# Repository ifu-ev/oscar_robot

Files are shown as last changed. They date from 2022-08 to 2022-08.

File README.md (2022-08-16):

# oscar_robot

## Content

- [oscar_robot](#oscar_robot)
  - [Introduction](#introduction)
  - [<span style="color:red">**!!! CAUTION !!!**</span>](#-caution-)
  - [Knowledge requirement](#knowledge-requirement)
  - [Shopping-List](#shopping-list)
    - [Budget Build Parts](#budget-build-parts)
    - [Original Build Parts](#original-build-parts)
    - [Laser-cutted parts](#laser-cutted-parts)
    - [3-D printed parts](#3-d-printed-parts)
  - [Build your robot](#build-your-robot)
    - [Hardware installation](#hardware-installation)
      - [Budget Build](#budget-build)
      - [Original Build](#original-build)
  - [Setup software](#setup-software)
    - [Budget Build (Raspberry Pi)](#budget-build-raspberry-pi)
    - [Original Build (Intel NUC)](#original-build-intel-nuc)
    - [Connect to Oscar via SSH](#connect-to-oscar-via-ssh)
    - [Installing ROS](#installing-ros)
    - [OSCAR workspace](#oscar-workspace)
    - [Connect Gamepad](#connect-gamepad)
  - [Usage](#usage)
    - [Teleoperation](#teleoperation)
    - [Mapping](#mapping)
    - [Navigation](#navigation)
  - [Publishing own navigation goals](#publishing-own-navigation-goals)
  - [Credits](#credits)

## Introduction

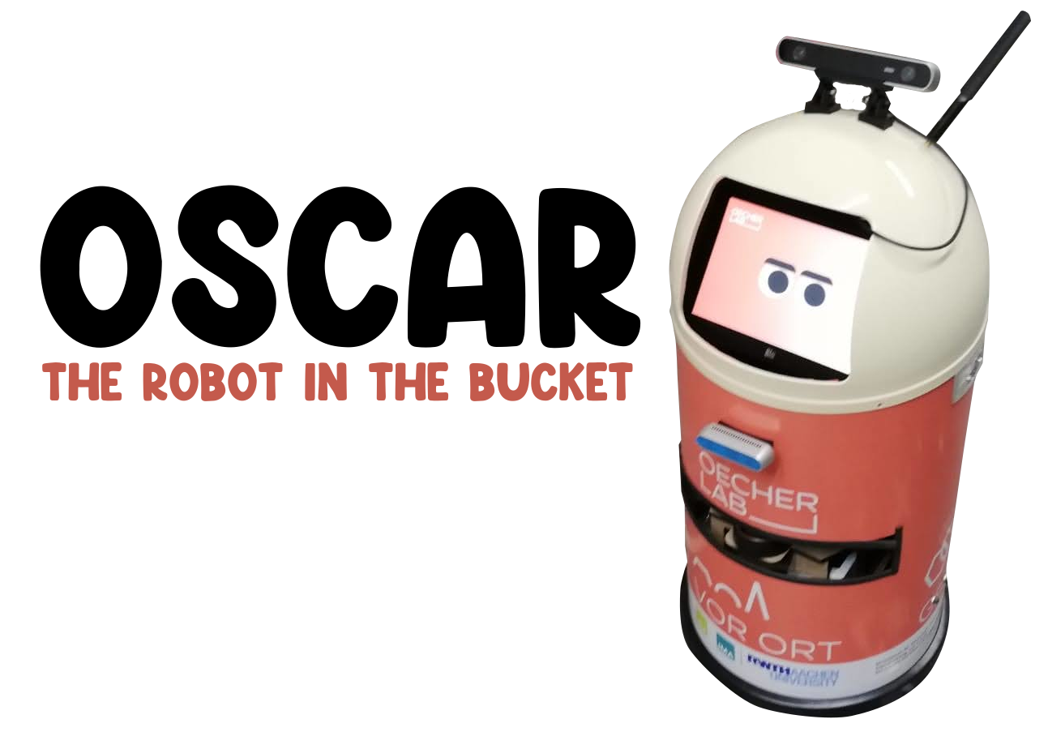
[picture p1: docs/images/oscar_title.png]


The "Oecher Lab" project is funded by the state of NRW, Germany as part of the "Digital Model Regions in NRW" program.

Oscar is a learning robot developed as part of the research project OecherLAB. Oscar is used to teach the Robot Operating System. It owes its name to its outer shell: the garbage can in which a well-known children's hero lives.

This documentation should enable everyone to rebuild and configure the robot, as well as to dare the first steps with ROS.

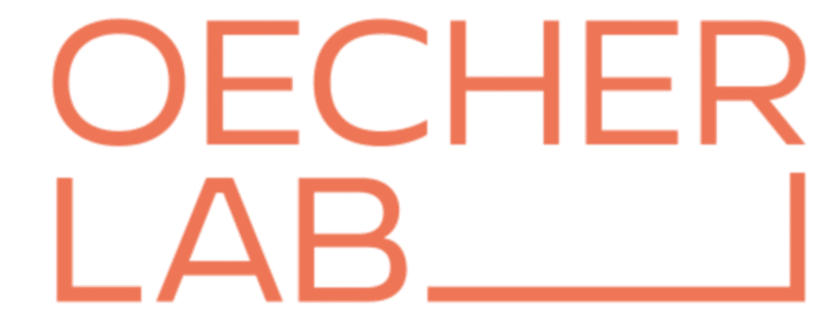
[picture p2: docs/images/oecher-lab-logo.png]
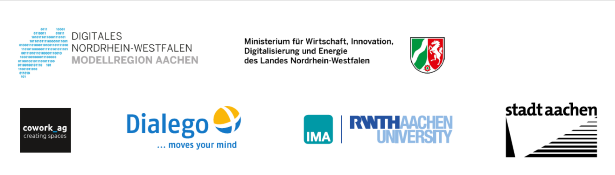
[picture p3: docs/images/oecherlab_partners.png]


https://user-images.githubusercontent.com/32275/184821746-e5f2bd64-7a9f-4834-b20b-766fcd85903a.mp4

<table class="tg">
<thead>
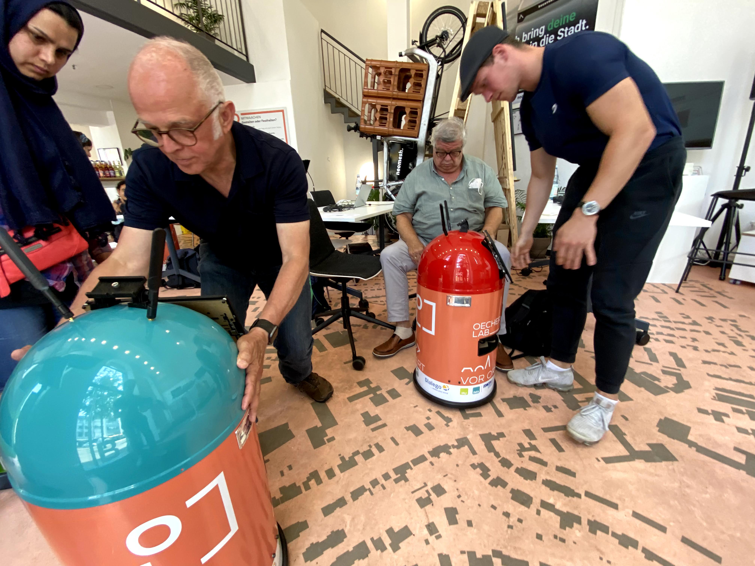
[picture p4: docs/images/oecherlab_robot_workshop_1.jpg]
    <td></td>
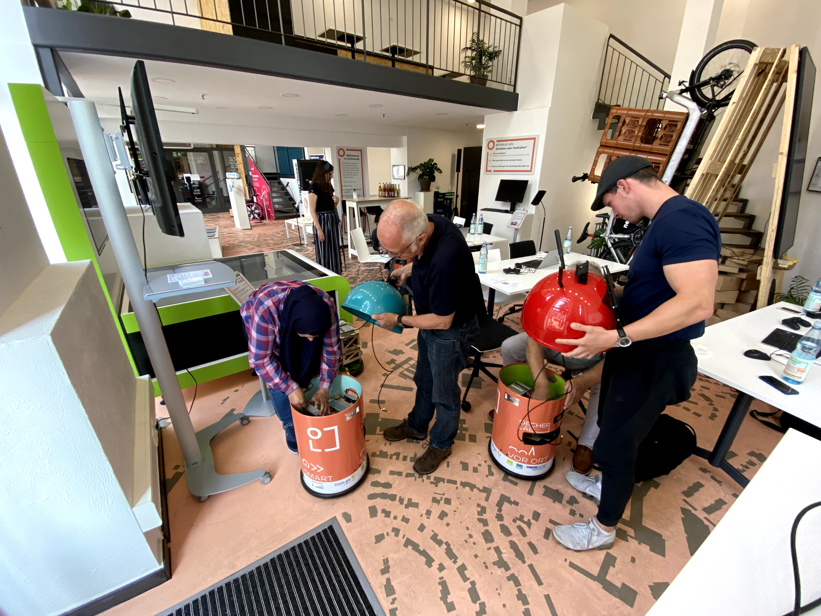
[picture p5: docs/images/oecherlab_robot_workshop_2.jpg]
    <td></td>
</thead>
</table>

---

## <span style="color:red">**!!! CAUTION !!!**</span>

**This tutorial contains instructions for working with electricity, soldering irons and sharp objects. Incorrect handling can lead to serious physical injuries. Please read about how to work safely with these topics before proceeding.**

---

## Knowledge requirement

- basic knowledge in Ubuntu Linux
- basic knowledge in ROS
- manual skills

## Shopping-List

In this chapter we describe the hardware you need to build your own Oscar. We build the Robot with powerful hardware to execute cutting edge algorithms (which are not part of this tutorial). If you just want to build the robot for getting in touch with ROS and the navigation stack, you can choose to build the budget build.

### Budget Build Parts

|Type | Product |
|-----|---|
|Robot Base|iRobot Create 2 (EOL/AfterMarket)|
|Embedded Computer|[RaspberryPi 4 (4GB)](https://www.google.de/search?tbm=shop&hl=de&q=raspberry+pi+4+4gb) + [64GB microSD Card (dont buy fakes from Aliexpress)](https://www.google.de/search?tbm=shop&hl=de&q=64GB+micro+SD+Card)|
|2D Lidar|[RPLidar A2M8](https://www.google.de/search?tbm=shop&hl=de&q=rplidar+a2m8)|
|RGBD Camera|[Intel Realsense d435i](https://www.google.de/search?tbm=shop&hl=de&q=realsense+d435i)|
|Gamepad|[Sony Dualshock 4 Controller](https://www.google.de/search?tbm=shop&hl=de&q=sony+dualshock+4)|
|DC/DC Converter|[Sunfounder Step-down DC-DC Converter Module for Raspberry Pi](https://www.robotshop.com/de/de/sunfounder-step-down-dc-dc-wandlermodul-raspberry-pi.html)|
|USB-C cable|[Generic USB-C Cable](https://www.google.de/search?tbm=shop&hl=de&q=usb-c+cable)|
|USB-A hub|[Generic USB-3.0-hub](https://www.google.de/search?tbm=shop&hl=de&q=usb+a+3.0+hub)|
|Battery|[Turnigy 5000mAh 6S LiPo](https://hobbyking.com/de_de/turnigy-5000mah-6s-40c-lipo-pack-xt90.html)|
|Charger|[Generic 6S LiPo Charger](https://www.google.com/search?q=lipo+charger+b6&source=lmns&tbm=shop)|
|Cable + Plug|[XT90 Plug (male) + cable](https://www.google.de/search?tbm=shop&hl=de&q=xt90+male+with+cable)|

### Original Build Parts

|Type | Product |
|-----|---|
|Robot Base|iRobot Create 2 (EOL/AfterMarket)|
|Roboter Body|[Wesco Pushboy](https://www.google.de/search?tbm=shop&hl=de&q=wesco+pushboy)|
|PC|[Intel NUC](https://www.google.de/search?tbm=shop&hl=de&q=intel+nuc+i5)  + [32GB DDR4-SODIMM 2666MHz](https://www.google.de/search?tbm=shop&hl=de&q=32gb+ddr4+sodimm+2666) + [512GB M2 SSD](https://www.google.de/search?tbm=shop&hl=de&q=32gb+ddr4+sodimm+2666)|
|AI PC|[Nvidia Jetson Nano](https://www.google.de/search?tbm=shop&hl=de&q=nvidia+jetson+nano)|
|Router|[Teltonika RUTX12](https://www.google.de/search?tbm=shop&hl=de&q=teltonika+rutx12)|
|2D Lidar|[RPLidar A2M8](https://www.google.de/search?tbm=shop&hl=de&q=rplidar+a2m8)|
|RGBD Camera|[Intel Realsense d435i](https://www.google.de/search?tbm=shop&hl=de&q=realsense+d435i)|
|Gamepad|[Sony Dualshock 4 Controller](https://www.google.de/search?tbm=shop&hl=de&q=sony+dualshock+4)|
|DC/DC Power Supply|[DCDC-USB, Intelligent DC-DC converter with USB interface](https://www.mini-box.com/DCDC-USB) + [Male DC Plug 5.5mm x 2.1mm](https://www.google.de/search?tbm=shop&hl=de&q=male+dc+plug)|
|Fuse Distribution Board|[Generic Distribution Board](https://www.google.de/search?tbm=shop&hl=de&q=fuse+distribution+board)|
|Molex cable|[Molex MicroFit Cable](https://www.google.de/search?tbm=shop&hl=de&q=4pin+molex+microfit+cable)|
|USB-C cable|[Generic USB-C Cable](https://www.google.de/search?tbm=shop&hl=de&q=usb-c+cable)|
|USB-A hub|[Generic USB-3.0-hub](https://www.google.de/search?tbm=shop&hl=de&q=usb+a+3.0+hub)|
|Ethernet Cable|[Ethernet Cable 0.4m](https://www.google.de/search?tbm=shop&hl=de&q=ethernet+cable)|
|WiFi Antenna Extension|[WiFi Antenna Extension](https://www.google.de/search?tbm=shop&hl=de&q=sma+extension)|
|Battery|[SLS 16000mAh 6S LiPo](https://www.stefansliposhop.de/akkus/sls-multirotor-uav/sls-xtron/sls-xtron-16000mah-6s1p-22-2v-20c-40c::2214.html)|
|Charger|[Generic 6S LiPo Charger](https://www.google.com/search?q=lipo+charger+b6&source=lmns&tbm=shop)|
|Cable + Plug|[XT90 Plug (male) + cable](https://www.google.de/search?tbm=shop&hl=de&q=xt90+male+with+cable)|

### Laser-cutted parts

The Create 2 base from iRobot has mounting points on its top plate. We use these points to attach a self developed lasercutted wooden construction. You can build your own top-construction for the raspberry pi/nuc and sensors, but we also provide the CAD files in the following table. You have to search for a company in your place to cut these parts for you.

Material thickness: 6 mm

| Qty | Type | Download |
|-----|---|---|
|1x|Layer bottom|[Download](docs/cad/layer_bottom.dxf)|
|1x|Layer middle|[Download](docs/cad/layer_middle.dxf)|
|1x|Layer top|[Download](docs/cad/layer_top.dxf)|
|3x|Side standard bottom|[Download](docs/cad/side_standard_bottom.dxf)|
|3x|Side standard top|[Download](docs/cad/side_standard_top.dxf)|
|1x|Side front bottom|[Download](docs/cad/side_front_bottom.dxf)|
|1x|Side front top|[Download](docs/cad/side_front_top.dxf)|

### 3-D printed parts

We provide a STL-File for mounting the Intel Realsense camera to the top plate. You have to print it by yourself or find a company in your area which can print it for you.

| Qty | Type | Download |
|-----|---|---|
|1x|Realsense mount|[Download](docs/cad/realsense_mount.stl)|

## Build your robot

To build your robot is quiet easy. You just have to slide the parts into each other. We recommend to fix the bottom connection of each side plate with hot glue. Screw the bottom plate on the item parts, which work as stands.

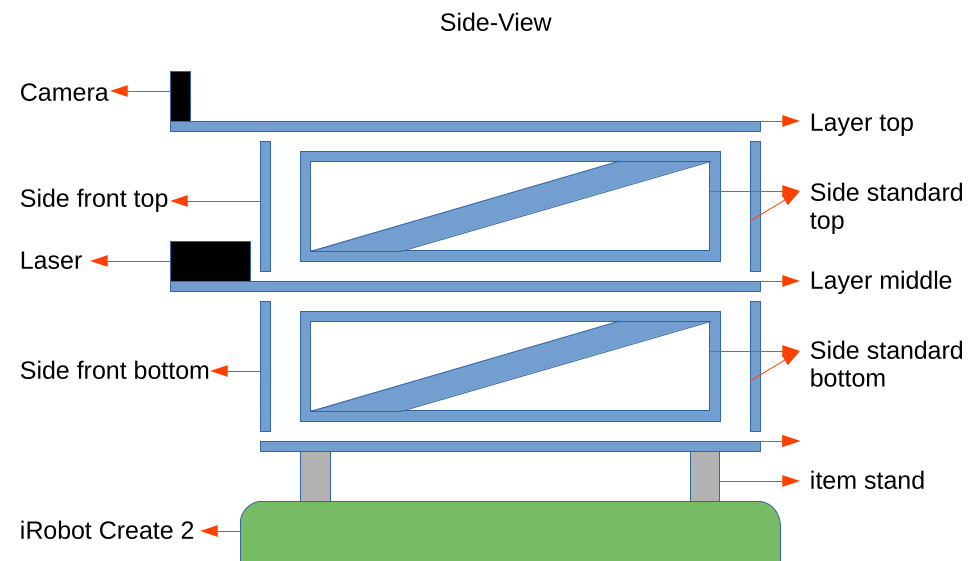
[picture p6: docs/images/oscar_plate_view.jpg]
oscar_plate_view


### Hardware installation

#### Budget Build

- Fix the raspberry pi on one of the layers.
- Connect the USB-C cable to the RaspberryPi and the DC/DC converter
- Prepare the XT90 with cable and connect it to the DC/DC converter
- Mount the Lidar on the front part of the middle plate with screws
- Screw the Realsense camera to the 3D-printed mounting and the mounting on the front of the top plate
- Connect both sensors and the iRobot Create Serial cable to the USB-Hub
- Connect the USB-Hub to the RaspberryPi
- Connect the battery to the DC/DC Converter when you want to run the robot

#### Original Build

- Install the RAM and SSD into the Intel NUC
- Fix the Intel NUC with the provided mounting plate (in package) to the "side standard top" with power button facing front
- Fix the Nvidia Jetson Nano on the middle plate
- Mount the Lidar on the front part of the middle plate with screws
- Screw the Realsense camera to the 3D-printed mounting and the mounting on the front of the top plate
- Mount the DC/DC Converter on the top plate
- Solder the XT90 with cables from package and connect it to the DC/DC converter
- Mount the fuse distribution board on bottom plate and connect the DC/DC converter
- Solder Cables with male DC plugs for powering Intel NUC and Nvidia Jetson Nano
- Connect the molex cable to the Teltonika RUTX12 and the distribution board
- Connect both sensors and the iRobot Create Serial cable to the USB-Hub
- Connect the USB-Hub to the Intel NUC
- Connect the battery to the DC/DC Converter when you want to run the robot
- Carefully remove the rivets holding the head together with the body of the pushboy using a small drill bit
- Use a lathe tool to cut a horizontal slit at the level of the RPLidar laser with an opening angle of approximately 160 degrees
- Cut a smaller opening for the Intel Realsense Camera on its height
- Drill a hole in the head for the SMA extension
- Hot-Glue the 3D-printed holders in the inside
- You can put the Pushboy on the Roomba as external chassy

## Setup software

- Install [Ubuntu 20.04 Desktop](https://releases.ubuntu.com/20.04/) on your local machine.

### Budget Build (Raspberry Pi)

- Download the [Raspbery Pi Imager](https://www.raspberrypi.com/software/)
- Start Imager
- Choose OS -> other general-purpose OS -> Ubuntu -> Ubuntu Server 20.04 LTS 64bit
- Insert the microSD into an SD Adapter and put it in your SD Card reader
- Choose Storage -> select microSD
- Click on the settings button
  - set hostname: oscar.local
  - enable ssh -> use password; username: oscar, pw: oscar
  - configure your local Wifi
  - configure your locale settings (timezone, keyboard)
  - save
- click on "Write"
- insert the sd card to your raspberry pi and turn it on
- the raspberry pi should connect to your wifi automatically

### Original Build (Intel NUC)

- Configure your [Teltonika RUTX12 to connect to your local Wifi](https://wiki.teltonika-networks.com/view/RUTX12)
- Download [Ubuntu 20.04 Desktop](https://releases.ubuntu.com/20.04/)
- Create a bootable USB Stick with your favourite flash tool (e.g. Rufus / Etcher)
- Put the stick in your Intel NUC
- Connect
- Connect a mouse, keyboard and monitor
- Start the Intel NUC and enter one-time boot menu
- Select the USB Drive in UEFI Mode
- Go through Ubuntu Installer
  - Username: oscar, pw: oscar
  - PC-Name: oscar

### Connect to Oscar via SSH

- Windows-User (you can connect via SSH, but you cannot visualize later on):
  - [Install PuTTY](https://www.chiark.greenend.org.uk/~sgtatham/putty/latest.html)
  - Start PuTTY
    - Host Name: oscar.local
    - Port: 22
  - Click "Open"
  - login as: `oscar`
- Linux-User:
  - Open your terminal (Ctrl + Shift + T)
  - `ssh oscar@oscar.local`
- Type in the password: `oscar` (passwords are not shown in the terminal)

### Installing ROS

- The next steps are slightly modified from original ROS installation ([ROS-WIKI](http://wiki.ros.org/noetic/Installation/Ubuntu))
- The commands have to be executed on the remote system over SSH connection AND on your local machine too (you have to do it twice)
  - `sudo sh -c 'echo "deb http://packages.ros.org/ros/ubuntu $(lsb_release -sc) main" > /etc/apt/sources.list.d/ros-latest.list'`
  - `sudo apt install curl`
  - `curl -s https://raw.githubusercontent.com/ros/rosdistro/master/ros.asc | sudo apt-key add -`
  - `sudo apt update && sudo apt dist-upgrade`
  - `sudo apt install ros-noetic-desktop-full`
  - `echo "source /opt/ros/noetic/setup.bash" >> ~/.bashrc`
  - `source ~/.bashrc`
  - `sudo apt install python3-rosdep python3-rosinstall python3-rosinstall-generator python3-wstool build-essential python3-catkin-tools vim screen`
  - `sudo rosdep init`
  - `rosdep update`
- We have to add the param `ROS_MASTER_URI` and `ROS_IP` to our `~/.bashrc` file on the remote and local machine
- Get the IPv4 of your remote and local machine
  - `ifconfig`
- Edit your `.bashrc`
  - `vim ~/.bashrc`
- Go to the bottom of the file with the arrow keys
- Enter Insert-Mode by hitting the key `i`
  - `ROS_MASTER_URI=http://<insert IP of NUC/Raspberry here>:11311` e.g. `ROS_MASTER_URI=http://192.168.0.100:11311`
  - `ROS_IP=<IP of the system you are working on>`
- Exit insert mode by hitting `ESC`
- Save your changes
  - `:wq` write and quit

### OSCAR workspace

- Now we install the oscar related packages and compile them
  - `mkdir -p ~/oscar_ws/src`
  - `cd ~/oscar_ws/src`
  - `git clone https://github.com/ifu-ev/oscar_robot`
  - `cd ..`
  - `rosdep install --from-paths src --ignore-src -r`
  - `catkin build`
  - `echo "source ~/oscar_ws/devel/setup.bash" >> ~/.bashrc`
  - `source ~/.bashrc`
  - `roscd oscar_bringup/udev`
  - `source create_udev_rules.sh`

### Connect Gamepad

- Connect to your remote machine via SSH
- Put your gamepad in pairing mode (Dualshock: Hold share and Playstation button until white light is flashing)
- `sudo bluetoothctl`
- `scan on`
- Wait until you see a Sony label
- `scan off`
- Copy the MAC address (this is an example mac address `4C:E9:9A:43:C7:2A`)
- `trust '<here your mac address'`
- `connect '<here your mac address'`
- The controller should be connected now

## Usage

To start the Oscar the ROS package oscar_bringup exists. In this package are all necessary launch files, which start the hardware drivers and the algorithms needed for the task.

### Teleoperation

- With the launch file `teleoperation.launch` the robot can be operated manually with the controller.
- `roslaunch oscar_bringup teleoperation.launch`

### Mapping

- With the launch file `mapping.launch` we can create a map for later autonomous navigation with the Oscar.
- Start the mapping on the remote machine
  - `roslaunch oscar_bringup mapping.launch`
- Start the Visualization on your local machine
  - `roslaunch oscar_bringup visualization.launch`
- Click on `2D Nav Goal` and set a goal pose on the map in the 3D view with your mouse
- The robot will move to that position
- The mapping algorithm is generating the map from the 2D lidar scanner
- We can use this map later for navigation tasks
- Save the map on your oscar robot
  - `roslaunch oscar_navigation save_map.launch`

https://user-images.githubusercontent.com/32275/184821308-42e46146-1e4e-4683-813a-816e334ea357.mp4

### Navigation

- After we have created a map of our environment, we can provide it to Navigation so that the path planning algorithm can take it into account in its calculation.
- Start `navigation.launch` on your robot to start the move_base navigation stack
  - `roslaunch oscar_bringup navigation.launch`
- Start the Visualization on your local machine
  - `roslaunch oscar_bringup visualization.launch`
- Click on `2D Pose Estimate` to give the localization algorithm a rough estimated position of your robot in the map
- Click on `2D Nav Goal` and set a goal pose on the map in the 3D view with your mouse

## Publishing own navigation goals

The ROS package `oscar_navigation` contains the ROS node [`pub_navpoints.py`](oscar_navigation/src/pub_navpoints.py) in the `src` folder. This is documented line by line and explains how to let the robot navigate to target positions without a GUI with just a few lines of code.

- First start the `navigation.launch` or `mapping.launch` bringup file
  - `roslaunch oscar_bringup navigation.launch` or `roslaunch oscar_bringup mapping.launch`
- Run the ROS node
  - `rosrun oscar_navigation pub_navpoints.py`

## Credits

- Tobias Brünker
- Christoph Henke
- Johanna Lauwigi
- Anna-Maria Meer
- Sebastian Reuter

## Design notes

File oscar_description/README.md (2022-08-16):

# oscar_description 

## Launch urdf robot description

```roslaunch oscar_description oscar.launch```

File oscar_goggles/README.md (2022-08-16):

# oscar_goggles

## Usage

```bash
roslaunch oscar_goggles oscar_goggles.launch camera_device:=0

```

## Arguments

- camera_device:=/dev/video<device_number>

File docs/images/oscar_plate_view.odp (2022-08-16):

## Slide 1

Side-View

Camera

Layer top

Side standard top

Layer middle

Side standard bottom

Side front top

Laser

Side front bottom

item stand

iRobot Create 2

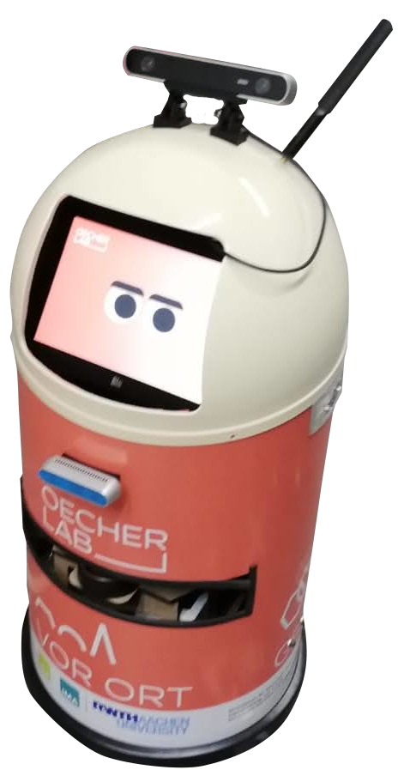
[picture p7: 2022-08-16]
docs/images/oscar.png

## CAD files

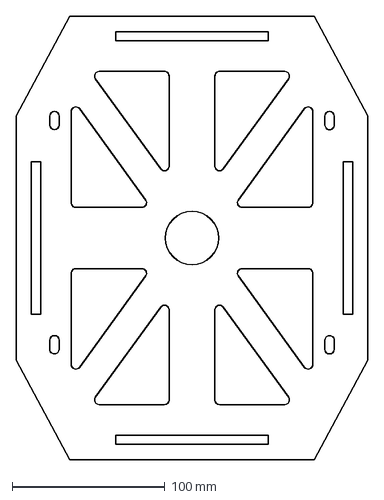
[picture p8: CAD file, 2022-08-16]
docs/cad/layer_bottom.dxf
230.0 x 290.0 mm

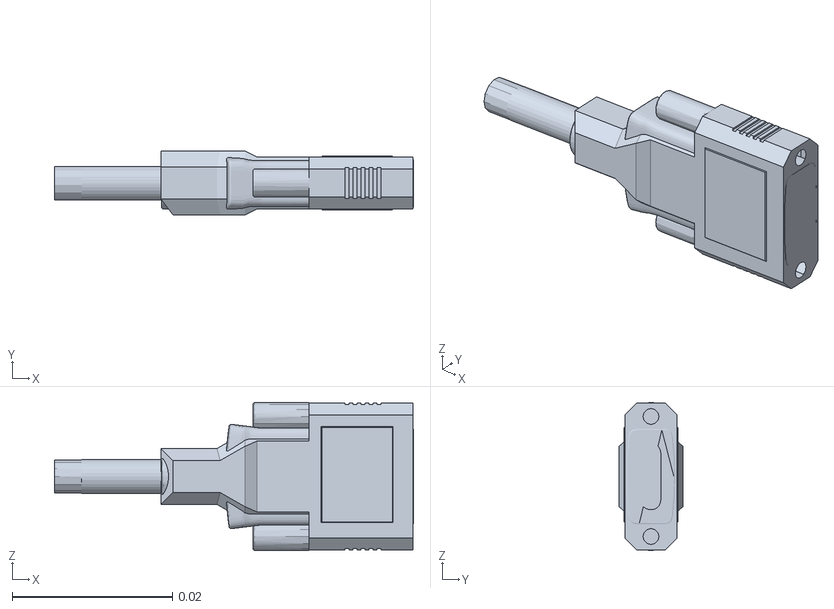
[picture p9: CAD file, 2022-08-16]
oscar_description/meshes/plug.stl
0.0448 x 0.008 x 0.0185

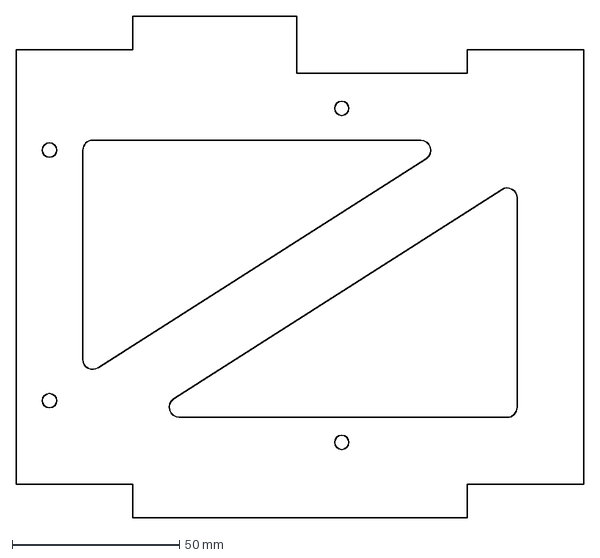
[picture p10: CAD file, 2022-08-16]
docs/cad/side_standard_top.dxf
170.0 x 150.0 mm

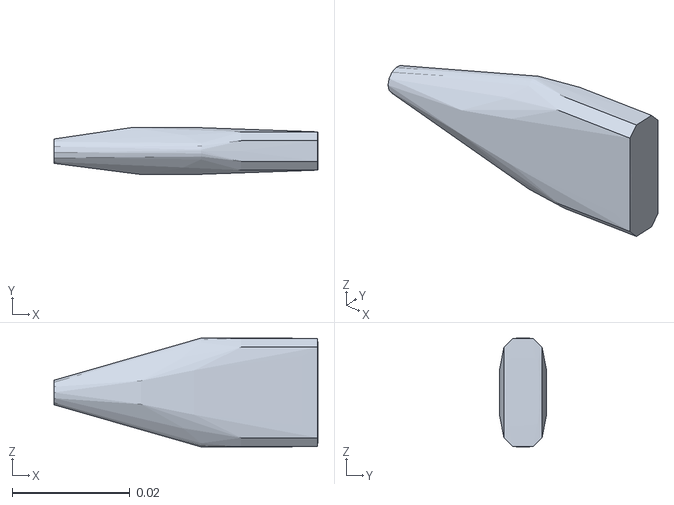
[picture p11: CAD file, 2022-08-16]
oscar_description/meshes/plug_collision.stl
0.0448 x 0.008 x 0.0185

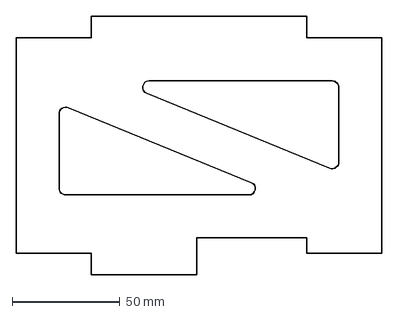
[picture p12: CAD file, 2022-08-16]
docs/cad/side_standard_bottom.dxf
170.0 x 120.0 mm

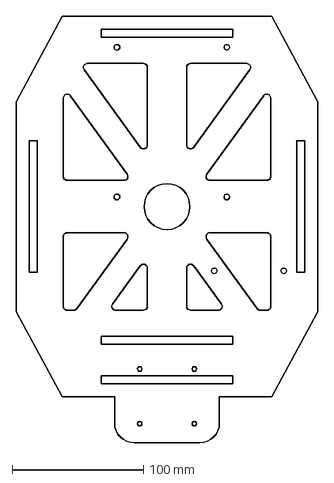
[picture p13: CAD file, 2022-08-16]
docs/cad/layer_middle.dxf
230.0 x 325.0 mm

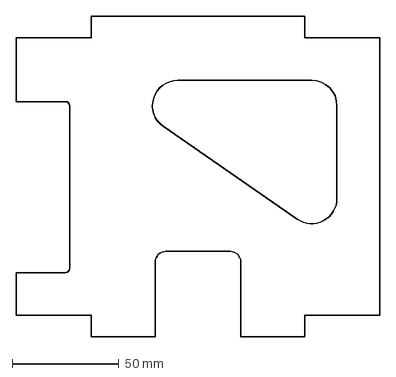
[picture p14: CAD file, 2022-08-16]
docs/cad/side_front_top.dxf
170.0 x 150.0 mm

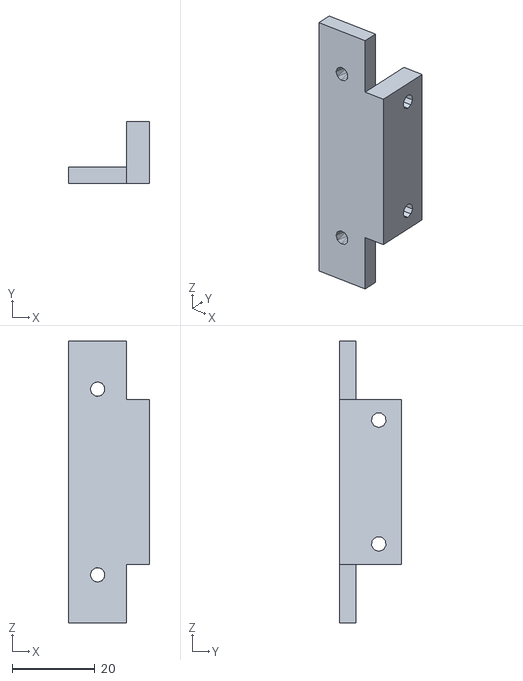
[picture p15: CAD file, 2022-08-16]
docs/cad/realsense_mount.stl
19.5 x 15.0 x 68.3

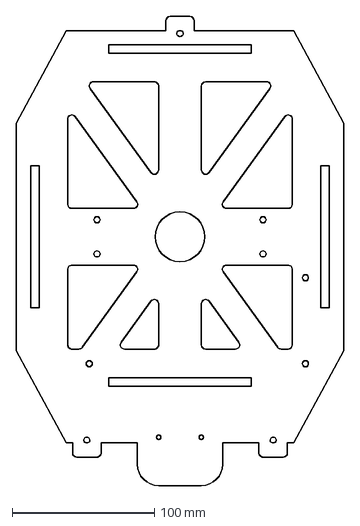
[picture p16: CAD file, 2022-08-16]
docs/cad/layer_top.dxf
230.0 x 330.0 mm

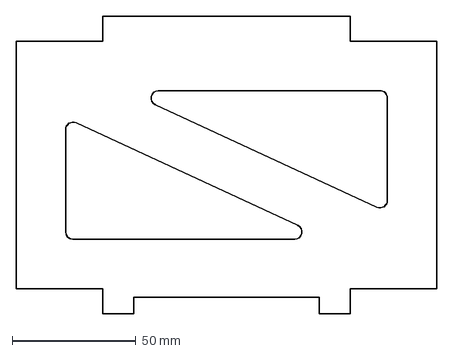
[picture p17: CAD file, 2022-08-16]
docs/cad/side_front_bottom.dxf
170.0 x 120.0 mm

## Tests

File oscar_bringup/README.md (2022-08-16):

# oscar Launch 

## First time use - configuration to use sick LIDAR:
Insert IP of LIDAR to your launch file:

```nano ~/oscar_ws/src/oscar_base/sick_scan/launch/sick_tim_5xx.launch```

Change the default value of arg name="hostname" to your LIDAR IP address

Set static IP address for ethernet on your computer in the same addressspace as the LIDAR. 
For example: LIDAR -> 192.168.0.10, Computer -> Adress: 192.168.0.102, Netmask: 255.255.0.0, Gateway:192.168.0.102

## First time use - configuration to use Roomba: 

USB Permission: 

```sudo usermod -a -G dialout $USER```
 
Restart 

## Install

Install ds4drv to connect to Ps4 controllers:```sudo pip install ds4drv```

## Launch
Disconnect the Ps4 controllers from any cable. 
Run ds4dr to connect to Ps4 controllers: ```sudo ds4drv```
Press the "share" button and the small black button with the Playstation symbol simultanously on the controller until you see white lights. 
Wait until the terminal informs you, that the controller is connected. 

Launch robot with Ps4 controllers:

```roslaunch oscar_launch joy_teleop_roomba_sick.launch```
